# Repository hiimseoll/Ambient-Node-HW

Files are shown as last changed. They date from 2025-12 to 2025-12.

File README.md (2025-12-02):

# Ambient-Node-HW - Fan and Axis control

Seeeduino XIAO RP2040을 사용해 BLDC모터 와 스텝모터 2개를 이용해 얼굴 추적, 자동 회전, 자연풍, 수동 조작 기능을 구현한 Ambient node 하위 HW프로젝트

한림대학교 25년도 2학기 SW캡스톤디자인

## Demo & Hardware

| | | |
|:---:|:---:|:---:|
|  |  |  |
| pan 테스트1 | pan 테스트2 | tilt 테스트1 |
|  |  |  |
| pan-tilt 테스트1 | pan-tilt 테스트2 | fan 테스트1 |
|  |  |  |
| fan 테스트2 | fan 테스트3 | fan-pan-tilt 테스트 |
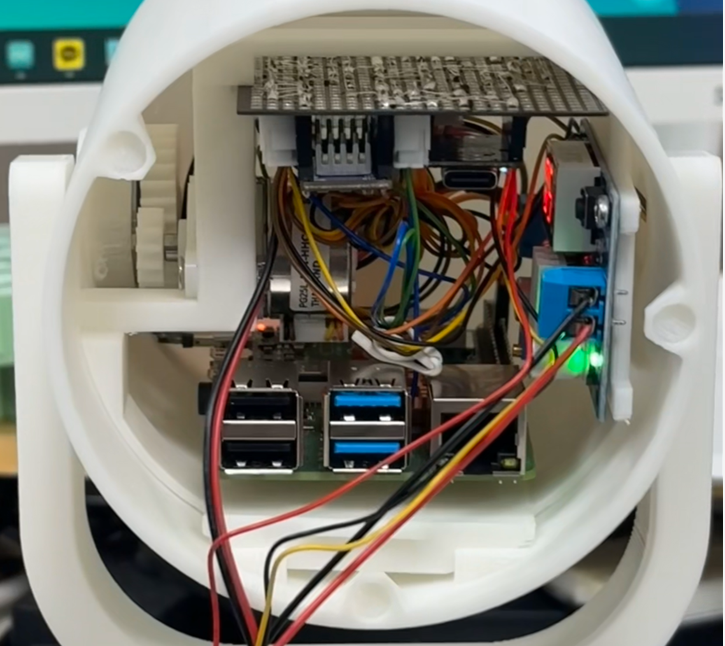
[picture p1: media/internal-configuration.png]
|  |  |  |
| 솔더링 플랜 | 솔더링 후 | 내부 구성 |

---

<p align="center">
  <a href="https://youtu.be/Y34z0qJ4gto">
    
  </a>
</p>
<p align="center">프로젝트 데모 영상</p>

## 하드웨어 구성

- MCU: seeduino XIAO RP2040
  - 초기에는 Seeeduino XIAO SAMD21을 사용했으나, BLDC 선풍기 제어에 필요한 20~60kHz 대역 고주파 PWM을 안정적으로 출력하기 어려워 제어용 보드를 XIAO RP2040으로 변경
  - RP2040은 PWM 대역이 유연하여 BLDC 팬용 고주파 PWM 신호 발생에 적합

- 스텝모터 2축 구성  
  - 모터1 (PAN, 좌우)  
    - STEP: D1  
    - DIR: D10  
    - EN: D2 (HIGH = 비활성화, LOW = 활성화)  
    - 소프트웨어 위치 범위: -10000 ~ +10000 스텝
  - 모터2 (TILT, 상하)  
    - STEP: D4  
    - DIR: D3  
    - EN: D5 (HIGH = 비활성화, LOW = 활성화)  
    - 소프트웨어 위치 범위: 0 ~ 8500 스텝 (0 = HOME)

- BLDC 선풍기 구성 
  - PWM 제어: D8 사용. 약 30Khz 고주파 PWM을 출력하며 듀티를 조정해 속도를 제어
  - FG(홀 센서) 입력: D9 사용. 인터럽트로 펄스를 카운트하여 RPM 계산.

- 기타 인터페이스 구성 
  - Serial: USB 디버그 및 테스트 명령 수신에 사용. 
  - Serial1: 얼굴 인식/좌표 및 제어 명령 수신용 UART로 사용.

## 보드 변경 배경

- XIAO SAMD21 사용 시 제약사항 
  - 기본 PWM 주파수가 낮고 타이머/채널 제약이 존재하여 BLDC 팬이 요구하는 20~60kHz 고주파 PWM을 안정적으로 구현하기 어려움. 
  - 타이머 레지스터 직접 제어를 통해 이론상 수십 kHz PWM 생성은 가능하나, 시스템 타이머(millis, delay 등) 및 다른 기능과 충돌 가능성이 존재함.  
  - 여러 채널에서 동일한 주파수·해상도를 유지하기 어렵고, 실제 팬 구동 시 특정 구간에서 소음, 떨림, 불안정한 구동이 발생할 수 있음.

- XIAO RP2040 선택 이유
  - RP2040은 다수의 PWM 채널을 제공하며, 고주파 PWM을 안정적으로 생성할 수 있음.  
  - 본 프로젝트에서는 BLDC 팬 구동용 PWM을 20~60kHz 대역으로 설정하기 위해 보드를 XIAO RP2040으로 변경.
  - XIAO RP2040은 Seeeduino XIAO(SAMD21)와 동일한 핀아웃과 폼팩터를 가지므로, 기존 PCB 설계를 수정하지 않고 그대로 사용할 수 있음.  
  - 보드 변경 이후 BLDC, 스텝모터, 고속 시리얼 통신을 동시에 사용해도 전체 시스템이 안정적으로 동작함.

## 주요 기능

### 얼굴 추적(페이스 트래킹) 기능

- 얼굴 좌표를 Serial1로 수신하여 선풍기 헤드를 얼굴 방향으로 회전시키는 기능
- 카메라 해상도는 1920 x 1080 기준으로 동작
  
- 명령 형식(Serial1)
  - `P (x,y)` 형식을 사용
    - 예: `P (960,540)` 형태로 사용

- 동작 방식 
  - 입력된 x, y 좌표를 기준으로 PAN/TILT 목표 스텝(target_motor1_pos, target_motor2_pos)을 계산. 
  - P 제어와 딜레이 스무딩을 사용하여 모터 속도를 조정.
  - TRACKING_DEADZONE 범위 내에서는 출력 명령을 억제하여 중앙 부근에서의 미세 떨림을 방지.

- 추적 정지 방식 
  - `P X` 또는 `P x` 명령을 수신하면 페이스 트래킹이 비활성화됨.  
  - 스텝모터 EN 핀을 HIGH로 설정하여 전류를 차단하고, 모터2 현재 위치를 EEPROM에 저장.

### BLDC 풍속 제어 기능

- 고정 풍량 모드 
  - 명령 형식(Serial1): `S n` (0~5) 사용. 
    - 0: 정지 또는 최소 풍량 수준으로 동작.
    - 1~5: SPEED_LEVELS 테이블에 정의된 PWM 값으로 속도를 설정.

- 자연풍 모드
  - 명령 형식(Serial1):  
    - `N 1` : 자연풍 모드 활성화
    - `N 0` : 자연풍 모드 비활성화 
  - NATURAL_WIND_MIN_LEVEL ~ NATURAL_WIND_MAX_LEVEL 범위 내에서 풍속 레벨을 주기적으로 증감시키며 자연스러운 풍량 변화를 구현
  - setBldcSpeed()와 updateBldcSpeed()를 통해 targetBldcPwm까지 1씩 보간하여 목표 PWM으로 서서히 수렴하도록 구현

- FG 기반 RPM 측정
  - BLDC_FG_PIN 인터럽트에서 fgPulseCount를 증가시키는 방식으로 펄스를 카운트
  - FG 3펄스를 1회전으로 가정하여 1초마다 RPM을 계산

### 자동 왕복 회전 모드 (좌우 자동 스윙)

- 명령 형식(Serial1) 
  - `R 1` : 회전 모드 활성화
  - `R 0` : 회전 모드 비활성화

- 동작 방식
  - 모터1(PAN)을 MOTOR1_MIN_STEPS ~ MOTOR1_MAX_STEPS 범위 내에서 왕복 회전시키는 기능 
  - 한쪽 끝에 도달하면 ROTATION_PAUSE_MS 동안 정지 후 회전 방향을 반전
  - 회전 모드 활성화 시 얼굴 추적 및 수동 조작 모드는 자동으로 비활성화

### 수동 조작 모드 (리모컨/버튼 대응)

- 명령 형식(Serial1, `A d state`)  

  - 모터1 (좌우) 제어  
    - `A r 1` : 오른쪽으로 수동 이동 시작
    - `A r 0` : 오른쪽 이동 정지
    - `A l 1` : 왼쪽으로 수동 이동 시작
    - `A l 0` : 왼쪽 이동 정지

  - 모터2 (상하) 제어
    - `A u 1` : 위쪽으로 수동 이동 시작
    - `A u 0` : 위쪽 이동 정지
    - `A d 1` : 아래쪽으로 수동 이동 시작
    - `A d 0` : 아래쪽 이동 정지

- 특징
  - 수동 모드 진입 시 facetracking 및 rotation_mode 플래그를 자동으로 비활성화하여 수동 조작이 최우선으로 동작 
  - 각 모터는 소프트웨어 위치 제한(MIN/MAX/HOME)을 항상 체크하여 허용 범위 밖으로 이동하지 않도록 구현
  - 모터2는 수동 이동 후 motor2_needs_save 플래그를 설정하고, 일정 시간이 지난 후 EEPROM에 위치가 자동 저장

### 단발 테스트 이동 (USB Serial 전용)

- 명령 형식(USB Serial) 
  - `1 cw 1000`  
  - `2 ccw 500`

- 동작 방식
  - 입력 문자열에서 모터 번호, 방향(cw/ccw), 스텝 수를 파싱하여 test_motor1_steps, test_motor2_steps 변수에 기록
  - loop에서 driveTestMotors()를 통해 지정된 스텝 수만큼만 이동하도록 동작
  - 이동 중에도 MIN/MAX/HOME 위치 제한을 적용
  - 테스트 이동 종료 후 EN 핀을 HIGH로 설정하여 모터 전류를 차단

### 모터 전원 관리 및 위치 저장

- EN 핀 로직
  - EN = LOW : 모터 드라이버 활성화(전류 인가, 홀딩 토크 유지) 
  - EN = HIGH : 모터 드라이버 비활성화(전류 차단, 발열 감소)

- 자동 전원 OFF 기능  
  - 마지막 스텝 이후 ENABLE_OFF_DELAY_MS 이상 동작이 없을 경우 EN을 HIGH로 설정하여 모터 전류를 자동 차단  
  - 수동 조작, 테스트 이동, 회전 모드, 얼굴 추적이 모두 비활성화된 상태에서만 적용

- 모터2 위치 EEPROM 저장
  - motor2_position은 MotorPosition 구조체(위치 값 및 유효 플래그) 형태로 EEPROM에 저장
  - motor2_position 변경 시 motor2_needs_save 플래그가 설정
  - 마지막 이동 후 EEPROM_SAVE_DELAY_MS가 경과하면 savePositionToFlash()를 호출하여 자동 저장 
  - 부팅 시 EEPROM에서 데이터를 읽어 VALID_SIGNATURE를 확인하고, 유효 시 해당 위치로 복원되며, 유효하지 않을 경우 HOME(0)으로 초기화 후 저장

### 디버그 및 유틸리티 기능

- USB Serial (Serial)
  - 그래프 모드  
    - `graph` 명령으로 그래프 디버그 모드를 토글
    - 활성화 시 Serial1로 "Time,Target,Current" 포맷의 데이터를 주기적으로 출력  
  - EEPROM 유틸리티  
    - `clear` : motor2_position을 초기화하고 유효 플래그를 제거
    - `sethome` : 현재 motor2_position을 HOME(0)으로 설정하고 EEPROM에 저장

- UART (Serial1) 사용
  - 얼굴 좌표 및 모든 제어 명령을 Serial1로 수신
  - 버퍼에 여러 줄이 쌓인 경우 가장 마지막 유효 명령만 처리하도록 구현

## 제어 로직 요약

- 모터 제어 우선순위는 다음과 같음.
  1. 수동 모터 조작 (A …)  
  2. 단발 테스트 스텝 이동 (1/2 cw/ccw …)  
  3. 자동 왕복 회전 (R 1)  
  4. 얼굴 추적 (P (x,y))

- loop 처리 흐름
  - 각 프레임마다 processUartCommand(), processDebugCommand()를 호출하여 명령을 처리
  - 우선순위에 따라 driveManualMotors(), driveTestMotors(), rotationMode(), faceTrackingControl() 중 하나를 실행.
  - checkMotorPowerOff(), naturalWindMode(), updateBldcSpeed(), checkAutoSave()를 호출하여 전원 관리, 자연풍 모드, BLDC 속도 보정, EEPROM 저장을 수행.
  - BLDC가 구동 중인 경우 measureRPM() 함수로 RPM을 주기적으로 측정

## 빌드 및 사용 방법

- Arduino IDE 보드 설
  - 보드: Seeed XIAO RP2040 보드 패키지 선택(https://github.com/earlephilhower/arduino-pico/releases/download/global/package_rp2040_index.json)
  - 시리얼 속도:  
    - USB Serial(Serial): 921600 사용함.  
    - UART(Serial1): 921600 사용함.

- 배선 및 업로드 절차  
  - 핀 정의에 맞게 스텝모터 드라이버와 BLDC 모터를 XIAO RP2040에 연결
  - 스케치를 업로드한 후 USB Serial 및 Serial1을 통해 동작을 검증

### 테스트 예시

- USB Serial(PC)에서 테스트
  - `1 cw 500`  
  - `2 ccw 500`

- Serial1(외부 장치)에서 제어
  - 얼굴 좌표: `P (960,540)`  
  - 얼굴 추적 정지: `P X`  
  - 풍속 설정: `S 3`  
  - 자연풍 모드: `N 1`  
  - 회전 모드: `R 1`  
  - 수동 조작: `A r 1`, `A r 0`, `A u 1`, `A u 0` 등 사용

## 주의사항 및 팁

- EN 핀 HIGH가 비활성화(전류 차단) 상태이므로, 구동 중이 아닐 때 EN을 HIGH로 유지하면 모터 발열이 감소됨.  
- 얼굴 추적, 자동 회전, 수동 조작 모드는 동시에 동작하지 않도록 상호 배타적으로 설계됨.  
- 모터2는 틸트 각도를 유지하기 위해 EEPROM에 위치를 저장. EEPROM_SAVE_DELAY_MS를 통해 저장 간격을 조절하여 EEPROM 수명을 보호.

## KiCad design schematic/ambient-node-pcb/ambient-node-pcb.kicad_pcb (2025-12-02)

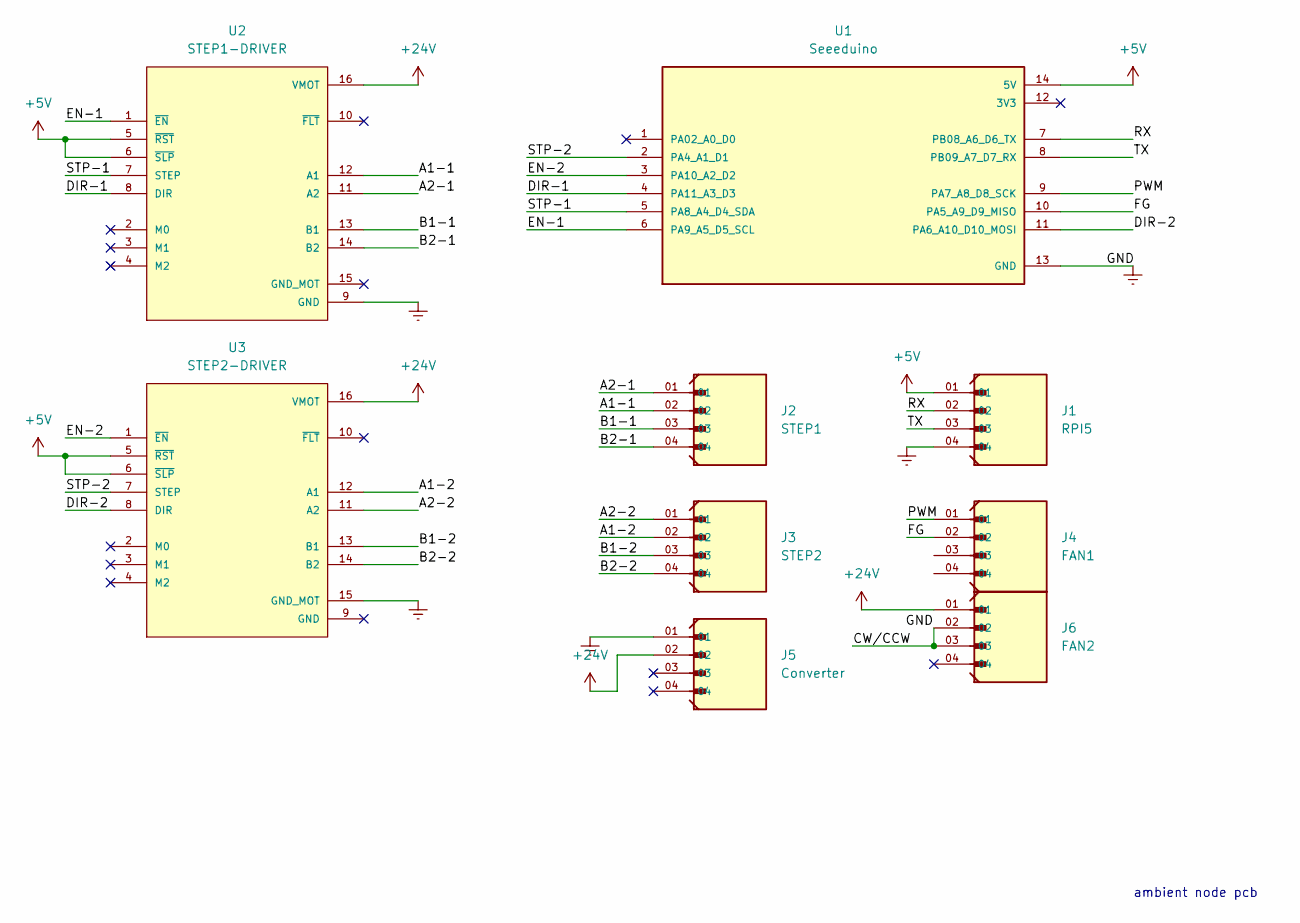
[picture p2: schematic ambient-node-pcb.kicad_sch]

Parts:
J1: RPI5; WURTH_61300411121
J2: STEP1; WURTH_61300411121
J3: STEP2; WURTH_61300411121
J4: FAN1; WURTH_61300411121
J5: Converter; WURTH_61300411121
J6: FAN2; WURTH_61300411121
U1: Seeeduino; MODULE_102010388; PARTREV N/A; DigiKey_Part_Number 1597-102010388-ND
U2: STEP1-DRIVER; IC_DRV8825_STEPPER_MOTOR_DRIVER_CARRIER
U3: STEP2-DRIVER; IC_DRV8825_STEPPER_MOTOR_DRIVER_CARRIER

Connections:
+5V: J1.01, U1.14 (5V), U2.5 (~RST), U2.6 (~SLP), U3.5 (~RST), U3.6 (~SLP)
+24V: J5.02, J6.01, U2.16 (VMOT), U3.16 (VMOT)
/A1-1: J2.02, U2.12 (A1)
/A1-2: J3.02, U3.12 (A1)
/A2-1: J2.01, U2.11 (A2)
/A2-2: J3.01, U3.11 (A2)
/B1-1: J2.03, U2.13 (B1)
/B1-2: J3.03, U3.13 (B1)
/B2-1: J2.04, U2.14 (B2)
/B2-2: J3.04, U3.14 (B2)
/DIR-1: U1.4 (PA11_A3_D3), U2.8 (DIR)
/DIR-2: U1.11 (PA6_A10_D10_MOSI), U3.8 (DIR)
/EN-1: U1.6 (PA9_A5_D5_SCL), U2.1 (~EN)
/EN-2: U1.3 (PA10_A2_D2), U3.1 (~EN)
/FG: J4.02, U1.10 (PA5_A9_D9_MISO)
/PWM: J4.01, U1.9 (PA7_A8_D8_SCK)
/RX: J1.02, U1.7 (PB08_A6_D6_TX)
/STP-1: U1.5 (PA8_A4_D4_SDA), U2.7 (STEP)
/STP-2: U1.2 (PA4_A1_D1), U3.7 (STEP)
/TX: J1.03, U1.8 (PB09_A7_D7_RX)
Earth: J1.04, J5.01, J6.02, J6.03, U1.13 (GND), U2.9 (GND), U3.15 (GND_MOT)

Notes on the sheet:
ambient node pcb

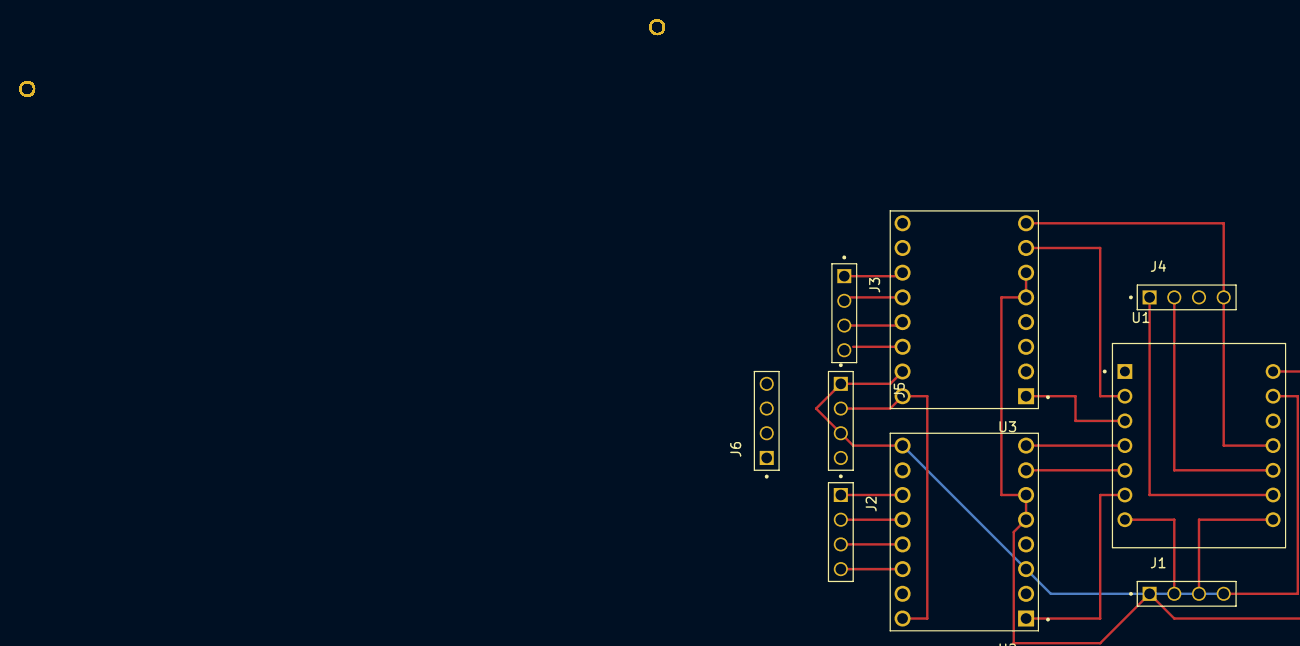
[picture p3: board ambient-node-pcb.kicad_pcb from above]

Board: 2 copper layers, 9 parts (0 on the bottom side), 21 nets.

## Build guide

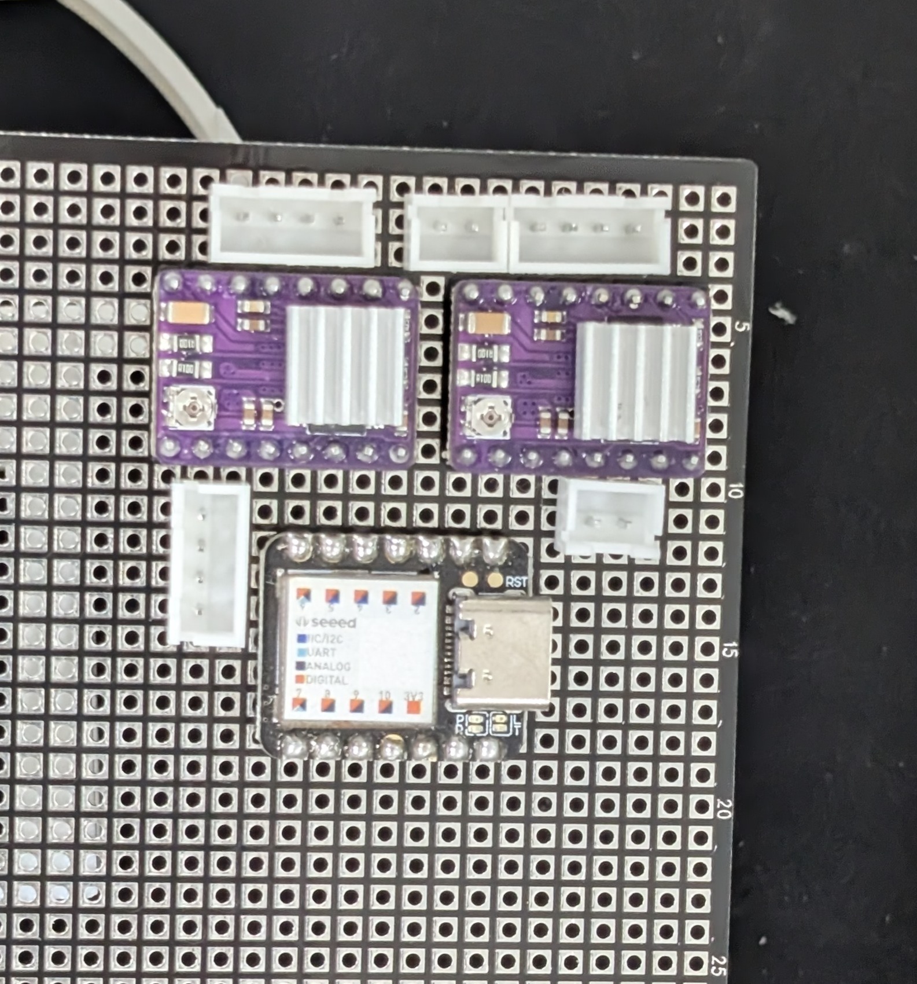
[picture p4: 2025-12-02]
media/before-soldering(plan).JPG

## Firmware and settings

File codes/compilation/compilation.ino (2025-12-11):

#include <EEPROM.h>

// 그래프 디버그 모드 플래그
bool graph_debug_mode = false;
unsigned long last_graph_print = 0;

// 카메라 해상도
#define CAM_WIDTH 1920
#define CAM_HEIGHT 1080

// 모터 동작 범위
const int MOTOR1_MIN_STEPS = -10000;
const int MOTOR1_MAX_STEPS = 10000;
const int MOTOR2_HOME = 0;
const int MOTOR2_MAX_STEPS = 8500;

// 스텝 딜레이 (속도 제어용)
#define MIN_DELAY_US 50
#define MAX_DELAY_US 800

// 페이스 트래킹 제어 게인
const float Kp = 3.5;
const float Ki = 0.02;
const int INTEGRAL_LIMIT = 500;

// 얼굴 위치 → 모터 이동 비율
const float PAN_GAIN = 3.0;
const float TILT_GAIN = 3.0;

// 추적 데드존 (중앙 근처 무시 구간)
#define TRACKING_DEADZONE 100

// 스텝 모터 전원 차단 지연
#define ENABLE_OFF_DELAY_MS 50

// EEPROM 자동 저장 지연
#define EEPROM_SAVE_DELAY_MS 3000

// 자연풍 레벨 범위 및 변경 주기
#define NATURAL_WIND_MIN_LEVEL 1
#define NATURAL_WIND_MAX_LEVEL 3
#define NATURAL_WIND_CHANGE_INTERVAL_MS 3000

// 회전 모드 방향 전환 대기시간
#define ROTATION_PAUSE_MS 1000

// 핀 정의
#define STEP_PIN2 D4
#define DIR_PIN2 D3
#define ENABLE_PIN2 D5
#define STEP_PIN1 D1
#define DIR_PIN1 D10
#define ENABLE_PIN1 D2
#define BLDC_PWM_PIN D8
#define BLDC_FG_PIN D9

// 모터 위치 저장용 구조체 (EEPROM)
typedef struct {
  int motor2_position; // 틸트 모터 현재 위치
  int valid;           // 유효 데이터 시그니처
} MotorPosition;

// 모터 위치 상태 값
int motor2_position = 0;
int motor1_position = 0;
const int VALID_SIGNATURE = 12345; // EEPROM 데이터 유효 여부 체크용 값

// EEPROM 저장 플래그 및 시간
bool motor2_needs_save = false;
unsigned long last_motor2_move_time = 0;

// BLDC 속도 상태
int bldcSpeedLevel = 0;
int currentBldcPwm = 255;
int targetBldcPwm = 255;
unsigned long lastBldcUpdate = 0;
// 속도 레벨별 PWM 값 테이블
const int SPEED_LEVELS[6] = {255, 176, 158, 138, 116, 70};

// FG 신호 기반 RPM 측정용 변수
volatile unsigned long fgPulseCount = 0;
unsigned long lastRpmTime = 0;
int currentRPM = 0;

// 수동 조작 상태 플래그
bool motor1_manual_moving = false;
bool motor2_manual_moving = false;
int motor1_manual_dir = 0;
int motor2_manual_dir = 0;

// 테스트 이동 명령용 변수
int test_motor1_steps = 0;
int test_motor1_dir = 0;
int test_motor2_steps = 0;
int test_motor2_dir = 0;

// 페이스 트래킹 상태 및 목표 위치
bool facetracking_enabled = false;
int target_motor1_pos = 0;
int target_motor2_pos = 0;

// 스텝 타이머 (비차단 제어용)
unsigned long lastStepTime1 = 0;
unsigned long lastStepTime2 = 0;

// PID 적분 항 (현재는 사용 거의 없음)
float integral_error_1 = 0;
float integral_error_2 = 0;

// 모터 동작 시각 기록
unsigned long last_motor1_action_time = 0;
unsigned long last_motor2_action_time = 0;

// 마지막 스텝 시간 (전원 자동 OFF 기준)
unsigned long last_motor1_step_time = 0;
unsigned long last_motor2_step_time = 0;

// 자동 왕복 회전 모드 상태
bool rotation_mode = false;
int rotation_direction = 1;

// 자연풍 모드 상태
bool natural_wind_mode = false;
unsigned long last_natural_wind_change = 0;
int natural_wind_target_level = 1;
bool natural_wind_increasing = true;

// 회전 모드 일시 정지 상태
unsigned long last_rotation_step = 0;
bool rotation_pausing = false;
unsigned long rotation_pause_start = 0;

// BLDC FG 인터럽트 콜백 (펄스 카운트)
void countFgPulse() { fgPulseCount++; }

void setup() {
  // BLDC 제어 핀 설정
  pinMode(BLDC_PWM_PIN, OUTPUT);
  digitalWrite(BLDC_PWM_PIN, HIGH);
  analogWriteFreq(30000);
  analogWriteRange(255);
  analogWrite(BLDC_PWM_PIN, 255);

  // 디버그 / 데이터용 직렬 포트
  Serial.begin(921600);
  Serial.setTimeout(2);
  Serial1.begin(921600);
  Serial1.setTimeout(2);

  // 스텝 모터 드라이버 Enable 핀
  pinMode(ENABLE_PIN1, OUTPUT);
  pinMode(ENABLE_PIN2, OUTPUT);
  digitalWrite(ENABLE_PIN1, HIGH); // 초기에는 비활성화
  digitalWrite(ENABLE_PIN2, HIGH);

  // 스텝 / 방향 핀 설정
  pinMode(STEP_PIN1, OUTPUT);
  pinMode(DIR_PIN1, OUTPUT);
  pinMode(STEP_PIN2, OUTPUT);
  pinMode(DIR_PIN2, OUTPUT);
  digitalWrite(STEP_PIN1, LOW);
  digitalWrite(DIR_PIN1, LOW);
  digitalWrite(STEP_PIN2, LOW);
  digitalWrite(DIR_PIN2, LOW);

  // BLDC FG 입력 및 인터럽트 설정
  pinMode(BLDC_FG_PIN, INPUT_PULLUP);
  attachInterrupt(digitalPinToInterrupt(BLDC_FG_PIN), countFgPulse, RISING);

  // EEPROM 초기화 및 모터 위치 로드
  EEPROM.begin(512);
  MotorPosition savedData;
  EEPROM.get(0, savedData);

  if (savedData.valid == VALID_SIGNATURE &&
      savedData.motor2_position >= MOTOR2_HOME &&
      savedData.motor2_position <= MOTOR2_MAX_STEPS) {
    motor2_position = savedData.motor2_position;
    Serial.print("Load Pos: ");
    Serial.println(motor2_position);
  } else {
    motor2_position = MOTOR2_HOME;
    savePositionToFlash();
  }

  Serial.println("Ready (High Speed 1/32 Tracking)");
  lastRpmTime = millis();
}

// 모터2 위치를 EEPROM에 저장
void savePositionToFlash() {
  MotorPosition dataToSave;
  dataToSave.motor2_position = motor2_position;
  dataToSave.valid = VALID_SIGNATURE;
  EEPROM.put(0, dataToSave);
  EEPROM.commit();
  Serial.println("Saved.");
}

// EEPROM 초기화 및 홈 위치로 리셋
void clearFlashMemory() {
  MotorPosition emptyData;
  emptyData.motor2_position = MOTOR2_HOME;
  emptyData.valid = 0;
  EEPROM.put(0, emptyData);
  EEPROM.commit();
  motor2_position = MOTOR2_HOME;
  motor2_needs_save = false;
  Serial.println("Cleared.");
}

// 일정 시간 지나면 모터2 위치 자동 저장
void checkAutoSave() {
  if (motor2_needs_save && (millis() - last_motor2_move_time >= EEPROM_SAVE_DELAY_MS)) {
    savePositionToFlash();
    motor2_needs_save = false;
  }
}

// BLDC 속도 레벨 설정
void setBldcSpeed(int level) {
  level = constrain(level, 0, 5);
  targetBldcPwm = (level == 0) ? 255 : SPEED_LEVELS[level];
  bldcSpeedLevel = level;
}

// BLDC PWM을 서서히 목표 값으로 보정
void updateBldcSpeed() {
  if (millis() - lastBldcUpdate >= 6) {
    if (currentBldcPwm < targetBldcPwm) currentBldcPwm++;
    else if (currentBldcPwm > targetBldcPwm) currentBldcPwm--;
    analogWrite(BLDC_PWM_PIN, currentBldcPwm);
    lastBldcUpdate = millis();
  }
}

// FG 펄스 기반 RPM 계산
void measureRPM() {
  if (millis() - lastRpmTime >= 1000) {
    if (bldcSpeedLevel > 0) {
      currentRPM = (fgPulseCount * 60) / 3; // FG 3펄스당 1회전 가정
      fgPulseCount = 0;
    }
    lastRpmTime = millis();
  }
}

// Serial1(UART) 명령 처리 (페이스 트래킹 / 속도 / 회전 / 수동 조작)
void processUartCommand() {
  if (Serial1.available() > 0) {
    String lastValidCommand = "";
    while (Serial1.available() > 0) {
      String temp = Serial1.readStringUntil('\n');
      temp.trim();
      if (temp.length() > 0) {
        lastValidCommand = temp;
      }
    }

    if (lastValidCommand == "") return;
    String input = lastValidCommand;

    // 얼굴 좌표(P (x,y)) → 목표 스텝으로 변환
    if (input.startsWith("P (")) {
      int openParen = input.indexOf('(');
      int commaIdx = input.indexOf(',');
      int closeParen = input.indexOf(')');
      if (openParen >= 0 && commaIdx > openParen && closeParen > commaIdx) {
        int px = input.substring(openParen + 1, commaIdx).toInt();
        int py = input.substring(commaIdx + 1, closeParen).toInt();
        px = constrain(px, 0, CAM_WIDTH);
        py = constrain(py, 0, CAM_HEIGHT);

        int error_x = px - (CAM_WIDTH / 2);
        int delta_step_1 = error_x * PAN_GAIN;
        target_motor1_pos = motor1_position + delta_step_1;
        target_motor1_pos = constrain(target_motor1_pos, MOTOR1_MIN_STEPS, MOTOR1_MAX_STEPS);

        int error_y = py - (CAM_HEIGHT / 2);
        int delta_step_2 = error_y * TILT_GAIN;
        target_motor2_pos = motor2_position + delta_step_2;
        target_motor2_pos = constrain(target_motor2_pos, MOTOR2_HOME, MOTOR2_MAX_STEPS);

        facetracking_enabled = true;
        rotation_mode = false;
        motor1_manual_moving = false;
        motor2_manual_moving = false;
      }
    }
    // 페이스 트래킹 정지
    else if (input == "P X" || input == "P x") {
      facetracking_enabled = false;
      digitalWrite(ENABLE_PIN1, HIGH);
      digitalWrite(ENABLE_PIN2, HIGH);
      if (motor2_needs_save) {
        savePositionToFlash();
        motor2_needs_save = false;
      }
      integral_error_1 = 0;
      integral_error_2 = 0;
    }
    // 고정 풍량 모드 (S n)
    else if (input.startsWith("S ")) {
      natural_wind_mode = false;
      setBldcSpeed(input.substring(2).toInt());
    }
    // 자연풍 모드 (N 1/0)
    else if (input.startsWith("N ")) {
      natural_wind_mode = (input.substring(2).toInt() == 1);
      if (natural_wind_mode) {
        natural_wind_target_level = NATURAL_WIND_MIN_LEVEL;
        natural_wind_increasing = true;
        last_natural_wind_change = millis();
      } else {
        setBldcSpeed(0);
      }
    }
    // 자동 왕복 회전 모드 (R 1/0)
    else if (input.startsWith("R ")) {
      int rMode = input.substring(2).toInt();
      facetracking_enabled = false;

      if (rMode == 1) {
        rotation_mode = true;
        rotation_direction = 1;
        digitalWrite(DIR_PIN1, HIGH);
        digitalWrite(ENABLE_PIN1, LOW);
        rotation_pausing = false;
      } else {
        rotation_mode = false;
        digitalWrite(ENABLE_PIN1, HIGH);
      }
    }
    // 수동 모터 제어 (A d state)
    else if (input.startsWith("A ")) {
      facetracking_enabled = false;
      rotation_mode = false;

      int firstSpace = input.indexOf(' ');
      int secondSpace = input.indexOf(' ', firstSpace + 1);
      if (firstSpace > 0 && secondSpace > 0) {
        char direction = input.charAt(firstSpace + 1);
        int state = input.substring(secondSpace + 1).toInt();
        // 좌우 조작
        if (direction == 'r' || direction == 'l') {
          if (state == 1) {
            motor1_manual_dir = (direction == 'r') ? 1 : 2;
            motor1_manual_moving = true;
            digitalWrite(DIR_PIN1, (direction == 'r') ? HIGH : LOW);
            digitalWrite(ENABLE_PIN1, LOW);
          } else {
            motor1_manual_moving = false;
            digitalWrite(ENABLE_PIN1, HIGH);
          }
        }
        // 상하 조작
        else if (direction == 'u' || direction == 'd') {
          if (state == 1) {
            motor2_manual_dir = (direction == 'u') ? 1 : 2;
            motor2_manual_moving = true;
            digitalWrite(DIR_PIN2, (direction == 'u') ? HIGH : LOW);
            digitalWrite(ENABLE_PIN2, LOW);
          } else {
            motor2_manual_moving = false;
            digitalWrite(ENABLE_PIN2, HIGH);
            motor2_needs_save = true;
            last_motor2_move_time = millis();
          }
        }
      }
    }
  }
}

// USB Serial 디버그 명령 처리
void processDebugCommand() {
  if (Serial.available() > 0) {
    String input = Serial.readStringUntil('\n');
    input.trim();
    if (input.length() == 0) return;

    // 그래프 출력 토글
    if (input == "graph") {
      graph_debug_mode = !graph_debug_mode;
      if(graph_debug_mode) Serial1.println("Time,Target,Current");
      else Serial1.println("Graph Mode OFF");
      return;
    }

    // EEPROM 초기화
    if (input == "clear") {
      clearFlashMemory();
      return;
    }
    // 현재 위치를 홈으로 설정
    if (input == "sethome") {
      motor2_position = MOTOR2_HOME;
      savePositionToFlash();
      return;
    }
    // 단발 테스트 이동 명령: "1 cw 1000" / "2 ccw 500" 등
    if (input.startsWith("1 ") || input.startsWith("2 ")) {
      int firstSpace = input.indexOf(' ');
      int secondSpace = input.lastIndexOf(' ');
      if (firstSpace > 0 && secondSpace > firstSpace) {
        int motorId = input.substring(0, firstSpace).toInt();
        String dirStr = input.substring(firstSpace + 1, secondSpace);
        int steps = input.substring(secondSpace + 1).toInt();
        int dirVal = (dirStr == "cw") ? 1 : -1;

        facetracking_enabled = false;
        rotation_mode = false;
        motor1_manual_moving = false;
        motor2_manual_moving = false;

        if (motorId == 1) {
          test_motor1_steps = steps;
          test_motor1_dir = dirVal;
        } else if (motorId == 2) {
          test_motor2_steps = steps;
          test_motor2_dir = dirVal;
        }
      }
    }
  }
}

// 테스트 이동 모드에서 지정된 스텝만큼 이동
void driveTestMotors() {
  unsigned long now_ms = millis();

  // 모터1 테스트 이동
  if (test_motor1_steps > 0) {
    bool canMove = true;
    if (test_motor1_dir == 1 && motor1_position >= MOTOR1_MAX_STEPS) canMove = false;
    if (test_motor1_dir == -1 && motor1_position <= MOTOR1_MIN_STEPS) canMove = false;

    if (canMove) {
      digitalWrite(ENABLE_PIN1, LOW);
      digitalWrite(DIR_PIN1, (test_motor1_dir == 1) ? LOW : HIGH);
      digitalWrite(STEP_PIN1, HIGH);
      delayMicroseconds(2);
      digitalWrite(STEP_PIN1, LOW);
      motor1_position += test_motor1_dir;
      last_motor1_step_time = now_ms;
    } else {
      digitalWrite(ENABLE_PIN1, HIGH);
    }

    delayMicroseconds(MIN_DELAY_US);
    test_motor1_steps--;

    if (test_motor1_steps == 0) digitalWrite(ENABLE_PIN1, HIGH);
  }

  // 모터2 테스트 이동
  if (test_motor2_steps > 0) {
    bool canMove = true;
    if (test_motor2_dir == 1 && motor2_position >= MOTOR2_MAX_STEPS) canMove = false;
    if (test_motor2_dir == -1 && motor2_position <= MOTOR2_HOME) canMove = false;

    if (canMove) {
      digitalWrite(ENABLE_PIN2, LOW);
      digitalWrite(DIR_PIN2, (test_motor2_dir == 1) ? LOW : HIGH);
      digitalWrite(STEP_PIN2, HIGH);
      delayMicroseconds(2);
      digitalWrite(STEP_PIN2, LOW);
      motor2_position += test_motor2_dir;
      motor2_needs_save = true;
      last_motor2_move_time = now_ms;
      last_motor2_step_time = now_ms;
    } else {
      digitalWrite(ENABLE_PIN2, HIGH);
    }

    delayMicroseconds(MIN_DELAY_US);
    test_motor2_steps--;

    if (test_motor2_steps == 0) digitalWrite(ENABLE_PIN2, HIGH);
  }
}

// 수동 조작 모드에서 연속 스텝 구동
void driveManualMotors() {
  const long MANUAL_STEP_DELAY = 50; // 수동 모드 스텝 간 딜레이
  unsigned long now_ms = millis();

  // 모터1 수동 이동
  if (motor1_manual_moving) {
    bool canMove = true;
    if (motor1_manual_dir == 1 && motor1_position <= MOTOR1_MIN_STEPS) canMove = false;
    if (motor1_manual_dir == 2 && motor1_position >= MOTOR1_MAX_STEPS) canMove = false;

    if (canMove) {
      digitalWrite(ENABLE_PIN1, LOW);
      digitalWrite(STEP_PIN1, HIGH);
      delayMicroseconds(2);
      digitalWrite(STEP_PIN1, LOW);
      motor1_position += (motor1_manual_dir == 1) ? -1 : 1;
      last_motor1_step_time = now_ms;
      delayMicroseconds(MANUAL_STEP_DELAY);
    } else {
      digitalWrite(ENABLE_PIN1, HIGH);
    }
  }

  // 모터2 수동 이동
  if (motor2_manual_moving) {
    bool canMove = true;
    if (motor2_manual_dir == 1 && motor2_position <= MOTOR2_HOME) canMove = false;
    if (motor2_manual_dir == 2 && motor2_position >= MOTOR2_MAX_STEPS) canMove = false;

    if (canMove) {
      digitalWrite(ENABLE_PIN2, LOW);
      digitalWrite(STEP_PIN2, HIGH);
      delayMicroseconds(2);
      digitalWrite(STEP_PIN2, LOW);
      motor2_position += (motor2_manual_dir == 1) ? -1 : 1;
      motor2_needs_save = true;
      last_motor2_move_time = millis();
      last_motor2_step_time = now_ms;
      delayMicroseconds(MANUAL_STEP_DELAY);
    } else {
      digitalWrite(ENABLE_PIN2, HIGH);
    }
  }
}

// 자동 왕복 회전 모드 제어
void rotationMode() {
  if (!rotation_mode) return;

  // 회전 방향 전환을 위한 일시 정지 구간
  if (rotation_pausing) {
    if (millis() - rotation_pause_start >= ROTATION_PAUSE_MS) {
      rotation_pausing = false;
      rotation_direction = (rotation_direction == 1) ? 2 : 1;
      digitalWrite(DIR_PIN1, (rotation_direction == 1) ? HIGH : LOW);
      digitalWrite(ENABLE_PIN1, LOW);
    } else {
      digitalWrite(ENABLE_PIN1, HIGH);
      return;
    }
  }

  // 범위 초과 시 방향 전환 준비
  bool hit_limit = false;
  if (rotation_direction == 1 && motor1_position <= MOTOR1_MIN_STEPS) hit_limit = true;
  if (rotation_direction == 2 && motor1_position >= MOTOR1_MAX_STEPS) hit_limit = true;

  if (hit_limit) {
    rotation_pausing = true;
    rotation_pause_start = millis();
    return;
  }

  // 일정 속도로 연속 스텝 (부드러운 회전)
  digitalWrite(ENABLE_PIN1, LOW);
  digitalWrite(STEP_PIN1, HIGH);
  delayMicroseconds(2);
  digitalWrite(STEP_PIN1, LOW);

  motor1_position += (rotation_direction == 1) ? -1 : 1;
  last_motor1_step_time = millis();

  delayMicroseconds(60);
}

// 자연풍 모드에서 속도 레벨을 주기적으로 변경
void naturalWindMode() {
  if (!natural_wind_mode) return;
  if (millis() - last_natural_wind_change >= NATURAL_WIND_CHANGE_INTERVAL_MS) {
    if (natural_wind_increasing) {
      if (++natural_wind_target_level >= NATURAL_WIND_MAX_LEVEL) natural_wind_increasing = false;
    } else {
      if (--natural_wind_target_level <= NATURAL_WIND_MIN_LEVEL) natural_wind_increasing = true;
    }
    setBldcSpeed(natural_wind_target_level);
    last_natural_wind_change = millis();
  }
}

// [수정됨] PI 제어 적용 + 소음 억제 기능 유지
void faceTrackingControl() {
  if (!facetracking_enabled) return;

  unsigned long now = micros();
  unsigned long now_ms = millis();

  // 속도 스무딩용 변수
  static float smooth_delay_1 = MAX_DELAY_US;
  static float smooth_delay_2 = MAX_DELAY_US;
  
  // 속도 고정용 변수 (주파수 떨림 방지)
  static long applied_delay_1 = MAX_DELAY_US;
  static long applied_delay_2 = MAX_DELAY_US;

  // 튜닝 파라미터
  const int SPEED_HYSTERESIS = 20; // 속도 변화 둔감화
  const float ACCEL_FACTOR = 0.05; // 부드러운 가속

  // ==================================================================================
  // [Motor 1 (X축) - PI Control]
  // ==================================================================================
  int error1 = target_motor1_pos - motor1_position;
  
  // 리밋 체크
  bool blocked1 = false;
  if (error1 > 0 && motor1_position >= MOTOR1_MAX_STEPS) blocked1 = true;
  if (error1 < 0 && motor1_position <= MOTOR1_MIN_STEPS) blocked1 = true;

  // 정지 조건 (데드존 내부이거나 리밋에 걸림)
  if (abs(error1) <= TRACKING_DEADZONE || blocked1) {
    // 1. 리밋/데드존 도달 시 전원 차단 (소음 제거)
    if (blocked1 || (now_ms - last_motor1_action_time > ENABLE_OFF_DELAY_MS)) {
      digitalWrite(ENABLE_PIN1, HIGH);
    }
    
    // 2. 적분값 서서히 감소 (Decay) - 갑작스런 튀는 동작 방지
    if (integral_error_1 > 0) integral_error_1 -= 1;
    else if (integral_error_1 < 0) integral_error_1 += 1;
    
    // 3. 속도 리셋
    smooth_delay_1 = MAX_DELAY_US; 
  } 
  else {
    // 이동 조건
    
    // [I 제어] 오차 누적
    integral_error_1 += error1;
    integral_error_1 = constrain(integral_error_1, -INTEGRAL_LIMIT, INTEGRAL_LIMIT);
    
    // [PI 제어 계산] 전역 변수 Kp, Ki 사용
    float control_signal = (Kp * error1) + (Ki * integral_error_1);
    
    // 속도 매핑
    long target_delay = map((long)abs(control_signal), 0, 1000, 1500, MIN_DELAY_US);
    target_delay = constrain(target_delay, MIN_DELAY_US, 1500);
    
    // 스무딩 (가속 제한)
    smooth_delay_1 = (smooth_delay_1 * (1.0 - ACCEL_FACTOR)) + (target_delay * ACCEL_FACTOR);
    
    // 속도 히스테리시스 (미세한 속도 변화 무시 -> 소음 감소)
    if (abs(smooth_delay_1 - applied_delay_1) > SPEED_HYSTERESIS) {
        applied_delay_1 = (long)smooth_delay_1;
    }

    // 스텝 출력
    if (now - lastStepTime1 >= applied_delay_1) {
      digitalWrite(ENABLE_PIN1, LOW); // 모터 켜기
      int dir = (error1 > 0) ? 1 : -1;
      
      digitalWrite(DIR_PIN1, (dir == 1) ? LOW : HIGH);
      digitalWrite(STEP_PIN1, HIGH);
      delayMicroseconds(2);
      digitalWrite(STEP_PIN1, LOW);
      
      motor1_position += dir;
      last_motor1_action_time = now_ms;
      last_motor1_step_time = now_ms;
      lastStepTime1 = now;
    }
  }

  // ==================================================================================
  // [Motor 2 (Y축) - PI Control]
  // ==================================================================================
  int error2 = target_motor2_pos - motor2_position;
  
  bool blocked2 = false;
  if (error2 > 0 && motor2_position >= MOTOR2_MAX_STEPS) blocked2 = true;
  if (error2 < 0 && motor2_position <= MOTOR2_HOME) blocked2 = true;

  if (abs(error2) <= TRACKING_DEADZONE || blocked2) {
    if (blocked2 || (now_ms - last_motor2_action_time > ENABLE_OFF_DELAY_MS)) {
      digitalWrite(ENABLE_PIN2, HIGH);
    }
    
    if (integral_error_2 > 0) integral_error_2 -= 1;
    else if (integral_error_2 < 0) integral_error_2 += 1;
    
    smooth_delay_2 = MAX_DELAY_US;
  } 
  else {
    // [I 제어]
    integral_error_2 += error2;
    integral_error_2 = constrain(integral_error_2, -INTEGRAL_LIMIT, INTEGRAL_LIMIT);
    
    // [PI 제어 계산]
    float control_signal = (Kp * error2) + (Ki * integral_error_2);
    
    long target_delay = map((long)abs(control_signal), 0, 1000, 1200, MIN_DELAY_US);
    target_delay = constrain(target_delay, MIN_DELAY_US, 1200);
    
    smooth_delay_2 = (smooth_delay_2 * (1.0 - ACCEL_FACTOR)) + (target_delay * ACCEL_FACTOR);

    if (abs(smooth_delay_2 - applied_delay_2) > SPEED_HYSTERESIS) {
        applied_delay_2 = (long)smooth_delay_2;
    }

    if (now - lastStepTime2 >= applied_delay_2) {
      digitalWrite(ENABLE_PIN2, LOW);
      int dir = (error2 > 0) ? 1 : -1;
      
      digitalWrite(DIR_PIN2, (dir == 1) ? LOW : HIGH);
      digitalWrite(STEP_PIN2, HIGH);
      delayMicroseconds(2);
      digitalWrite(STEP_PIN2, LOW);
      
      motor2_position += dir;
      motor2_needs_save = true;
      last_motor2_move_time = now_ms;
      last_motor2_action_time = now_ms;
      last_motor2_step_time = now_ms;
      lastStepTime2 = now;
    }
  }
  
  if (graph_debug_mode && (now_ms - last_graph_print >= 10)) {
    Serial1.print(now_ms);
    Serial1.print(",");
    Serial1.print(target_motor1_pos);
    Serial1.print(",");
    Serial1.println(motor1_position);
    last_graph_print = now_ms;
  }
}
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
void loop() {
  // 명령 수신 처리
  processUartCommand();
  processDebugCommand();

  // 모드 우선순위에 따른 모터 제어
  if (motor1_manual_moving || motor2_manual_moving) driveManualMotors();
  else if (test_motor1_steps > 0 || test_motor2_steps > 0) driveTestMotors();
  else if (rotation_mode) rotationMode();
  else if (facetracking_enabled) faceTrackingControl();

  // 전원 관리 및 부가 기능
  checkMotorPowerOff();
  naturalWindMode();
  updateBldcSpeed();
  checkAutoSave();

  // BLDC RPM 측정
  if (bldcSpeedLevel > 0) measureRPM();
}

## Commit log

2025-12-02 Add test.txt with initial content 'schematic'
2025-12-02 ambient node pcb - schematic
    [ambient-node-pcb.kicad_pcb, ambient-node-pcb.kicad_sch]
